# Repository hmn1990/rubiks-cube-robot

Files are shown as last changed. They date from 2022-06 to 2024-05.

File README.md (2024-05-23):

# 三阶魔方还原机器人

## 介绍
低成本魔方机器人设计。 含原理图、PCB、单片机源码（c语言）、结构图（openSCAD格式/STL格式）、主要器件BOM。 使用rp2040单片机控制，控制和魔方求解都使用单片机完成。 对于随机打乱的魔方，平均还原步骤数在21步左右。**扫描+计算+还原总时间在5.2秒左右。**  
2024-05-23主要更新内容：  
1.更换效率更高的魔方求解算法(感谢陈霜大神开源的min2phase，https://github.com/cs0x7f/min2phase.git)  
(1) 将使用java实现的min2phase改为使用c语言实现.  
(2) 测试10000个随机打乱的魔方,平均还原步骤数量由21.68步下降为20.25步.  
(3) 测试50个随机打乱的魔方,平均计算时间由180ms缩短为128ms.  
(4) 不需要NAND FLASH芯片W25N01,简化了设计,降低了成本.  
2.新增急停功能,在魔方还原过程中按下BUTTON_0或者1可以停止还原.  

2024-04-14主要更新内容：  
优化NAND FLASH刷写.刷写工具另开新仓库存放:  
https://gitee.com/hemn1990/uf2-nand-flash-prog  
以前的NAND FLASH刷写方式依旧可以使用.  
推荐使用新方式刷写NAND FLASH.  
新方式刷写时间更短,操作更简单.  

2024-03-28主要更新内容：  
优化求解魔方的程序,计算耗时减少1.5%.  
使用cube_robot.c里的debug_solve()测试  
STEP_LIMIT=23 P2_STEP_LIMIT_MAX=11 测试50个随机打乱的魔方，耗时8982ms  

2024-01-16主要更新内容：  
1.解决魔方安装错误时，容易死机的问题。  
2.修复使用还原功能后，立即使用自动测试功能，无法正确打乱魔方的问题。  
3.更新性能测试数据。  

2024-01-14主要更新内容：  
1.提升稳定性，可通过30轮的打乱+还原循环测试。测试30组不同的、使用CubeExplorer5.0的WCA打乱公式打乱的魔方，平均还原时间在5.2秒左右。作为对比，v2.0的平均还原时间在7.6秒左右。  
2.增加魔方打乱功能。  
3.增加打乱+还原自动测试功能  
4.移除无用还原动作。  
5.修改慢动作逻辑，操作方式改为短按SW4正常还原，长按SW4慢动作还原。  

2024-01-13主要更新内容：  
1.使用FIFO+PIO控制步进电机，支持三个电机以各自独立的速度曲线同时运动。  
2.改成只使用RP2040的一个核心，代码更容易被理解。  
3.提升I2C频率，顺便修复I2C1没有停止位的BUG。  
4.增加编译好的MCU固件cube_robot.uf2。  
5.优化还原速度，对每个动作设置各自独立的速度和加速度。  
6.优化还原速度，优化运动控制逻辑，支持同时执行某些动作，  

V2.0版本更新内容：  
1.提供原理图和PCB。  
2.解决滑台卡扣寿命短、容易断裂或者松动的问题，改为磁力固定。  
3.支持使用手机或者电脑的Type-C充电器供电。  
4.解决魔方夹持结构在长时间使用后容易松动、以及异常条件下可能断裂的问题。  
5.优化霍尔开关安装方式，简化安装步骤。  
6.解决棘轮结构噪声特别大的问题。  
7.提供详尽的装配教程，适合新手看的那种。  
8.完善物料清单。  
9.补充性能测试数据。  

后续更新计划：  
1.优化魔方还原算法。  

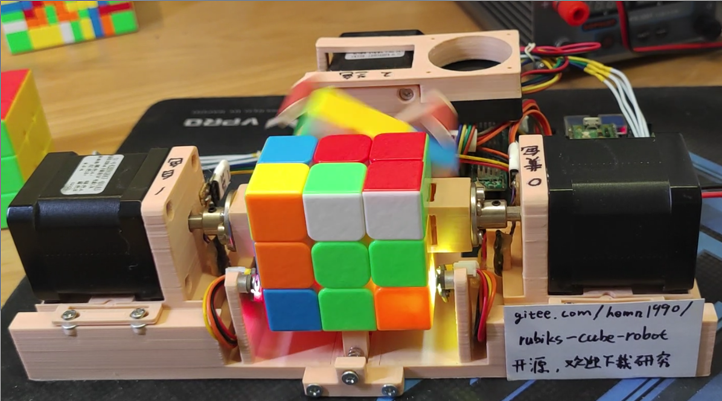
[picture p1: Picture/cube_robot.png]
Image text


V1.0版本演示视频：video/VID_20220618_165444.mp4  
V1.1版本（21步版本）的演示视频：http://www.bilibili.com/video/BV1Qt4y1476Y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  
V2.0版本的演示视频：https://b23.tv/s6q7KzU  
装配与调试教程：  
（1）控制板调试 https://b23.tv/Xj93aZk  
（2）魔方的选购 https://b23.tv/2x8Be0n  
（3）机械部分的组装 https://b23.tv/huJY1xt  
（4）整机调试 https://b23.tv/o8LBCXT  
（5）软件更新，10分钟搞定FLASH刷写 https://b23.tv/LJm5dEw  

## 关于硬件设计
2023-12-25更新：新增原理图与PCB设计文件  
2022-07-07更新：SPEPPER_EN修改为GP2，添加SPI NAND FLASH 型号W25N01GVZEIG  
2022-07-10更新：按键由GP0,GP1改为GP27,GP28)只修改了./src_21_step  

将RP2040单片机的GPIO，任意连接到步进电机驱动器、颜色传感器、霍尔传感器即可。除了SPI、UART，其他引脚只用了GPIO，未使用其他复用功能。  
霍尔传感器只能5V供电，RP2040单片机IO是3.3V，注意电平转换设计。  
FLASH是可选的，如果不使用FLASH，平均还原步骤数在32步左右。  
参考GPIO分配方式如下：  

#### 步进电机使能信号
- SPEPPER_EN    GP2
#### 步进电机控制信号
- SPEPPER_STEP0 GP11
- SPEPPER_DIR0  GP10
- SPEPPER_STEP1 GP9
- SPEPPER_DIR1  GP8
- SPEPPER_STEP2 GP7
- SPEPPER_DIR2  GP6
#### 霍尔开关，用于寻找零点
- HALL_0        GP5
- HALL_1        GP3
- HALL_2        GP4
#### 按键
- BUTTON_0      GP27
- BUTTON_1      GP28
#### 颜色传感器信号
- SDA0          GP14
- SCL0          GP15
- SDA1          GP12
- SCL1          GP13`
#### SPI NAND FLASH信号
- CS(1)         GP17
- DO(2)         GP16
- DI(5)         GP19
- CLK(6)        GP18

## 关于结构设计
1、推荐使用**ABS材料**3D打印，喷嘴0.4mm，层高0.2mm，顶层5层、底层5层、外壳4圈、填充20%-40%，生成支撑。  
## 单片机固件编译(./src_v3,平均还原步骤数在20步左右的版本，硬件上不需要外挂1Gbit FLASH)
修改CMakeLists.txt中的PICO_SDK_PATH，改为SDK的安装路径。  
````
# initalize pico_sdk from installed location
# (note this can come from environment, CMake cache etc)
set(PICO_SDK_PATH "/home/pi/pico/pico-sdk")
````
然后编译：  
````
cd ./src_v3/mcu
mkdir build
cd build
cmake ..
make
````
然后找到cube_robot.uf2，刷写到RP2040单片机即可。  
可以连接USB，使用minicom -D /dev/ttyACM0指令查看调试信息.  

## 单片机固件编译(./src_v2,平均还原步骤数在21步左右的版本)
推荐使用Linux系统进行开发，可按照RP2040官方文档中的脚本搭建开发环境。  
完成后，可额外安装pypy3，用于计算查找表。（此步骤可省略，提供生成好的）  
Windows也行，不过我没验证过。  

以Linux操作系统为例讲解,编译PR2040固件也可以使用Windows或者MacOS系统.  
参考raspberrypi官网搭建开发环境:  
https://www.raspberrypi.com/documentation/microcontrollers/rp2040.html  
也可以在b站搜索RP2040 SDK,找视频教程.  
搭建开发环境后,即可编译.  

**生成查找表**，并且进行验证（可选步骤,prog_flash目录下提供生成好的）  

运行完成后，得到lookup.dat,文件大小大约70MB  
````
cd ./src_v2/verify_on_pc
pypy3 prun.py
make
./solve
````

**编译单片机固件**
修改CMakeLists.txt中的PICO_SDK_PATH，改为SDK的安装路径。  
````
# initalize pico_sdk from installed location
# (note this can come from environment, CMake cache etc)
set(PICO_SDK_PATH "/home/pi/pico/pico-sdk")
````
然后编译：   
````
cd ./src_v2/mcu
mkdir build
cd build
cmake ..
make
````
然后找到cube_robot.uf2，刷写到RP2040单片机即可。  

可以连接USB，使用minicom -D /dev/ttyACM0指令查看调试信息，例如：  
````
color_detect: URUFUBDDUFRRFRDDFURLLLFUDLLLUBRDLRBFLDBDLBFFFBUBRBBRUD
Find 21 step solution in 139ms: B F' D' L' B F R B' U2 R B U2 B2 R2 U F2 D' B2 L2 U F2 
Totel time cost 7.772s: 
color_detect: UFFFURURRBDRRRDDLFBUDBFFBDFLBLLDBUBDFURLLRBUDUDLLBFRUL
Find 19 step solution in 95ms: F L2 B' R' L2 B L' B' F' D B2 D F2 D U B2 F2 L2 B2 
Totel time cost 7.575s: 

````
**刷写SPI NAND FLASH**
https://gitee.com/hemn1990/uf2-nand-flash-prog  
以前的NAND FLASH刷写方式依旧可以使用.  
推荐使用新方式刷写NAND FLASH.  
新方式刷写时间更短,操作更简单.  

以下为旧的方式：  
连接电脑和RP2040的串口，注意线一定要短，波特率高达1Mbps。   

按住BUTTON_0的同时给魔方机器人上电，程序会计算NAND FLASH的CRC32校验和，如果失败，自动进入刷写模式   
***注意烧写串口和USB虚拟串口不是同一个,不是同一个,不是同一个,重要的事情要说三遍.***   

````
cd ./src_21_step/prog_flash
make
./prog /dev/ttyS0 # /dev/ttyS0改为电脑的串口号

````
运行prog的电脑终端出现如下调试信息，说明刷写成功。
````
mcu in SPI FLASH programming mode
Check lookup.dat CRC32 = A8093698
0, size=131072
Erase Block 0
Program Block 0 ................................................................
Verify Block CRC32 0................................................................
此处省略若干行...
Erase Block 565
Program Block 565 ................................................................
Verify Block CRC32 565................................................................

````

## 单片机固件编译(./src_v1,平均还原步骤数在32步左右的版本，硬件上不需要外挂1Gbit FLASH)
*此版本不再维护，慎用*  
*与目前的硬件设计不完全匹配*  
推荐使用Linux系统进行开发，可按照官方文档中的脚本搭建开发环境。  
Windows也行，不过我没验证过。  

搭建好之后
````
cd src_v1
mkdir build
cd build
export PICO_SDK_PATH=xxxxxxxx
cmake ..
make
````
然后找到cube_robot.uf2，刷写到RP2040单片机即可。

可以连接USB，使用minicom -D /dev/ttyACM0指令查看调试信息，例如：
````
color_detect: FLDFUUUDBDLRURRFDLBFRDFBFLRDDURDBBUBLURBLRLBLFFUFBLDRU
stage=0, D' B U' L F' 
stage=1, B2 R2 U2 F2 D R' L' U L' 
stage=2, R2 D' F2 D2 R2 D R2 D' B2 D' 
stage=3, B2 R2 U2 B2 U2 L2 U2 L2 F2 R2 B2 
````

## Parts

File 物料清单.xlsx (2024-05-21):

整机物料：
物料名称 | 物料数量 | 备注
M3x6螺丝 | 12个 | 螺丝数量仅供参考，结构图没有绘制螺丝，可能有数漏的情况，建议多买些。 固定磁铁的4个必须用沉头的，其他的不限制。
M3x8螺丝 | 13个
M3x12螺丝 | 2个
M3x18螺丝 | 2个 | 固定风扇用的，有点长，M3x14更合适
M3滚花螺母(M3x4x5) | 11个 | 如果爪子部分使用3D打印+法兰联轴器，再加8个 外径5mm，螺纹M3，光杆直径4.3mm，高度4mm
M6垫片 | 4个 | 外径12mm，内径无所谓 必须选择能被磁铁吸引的材料，不能用不锈钢的
M3机米螺丝 | 6个 | 平头，3mm长度
直径2mm，长度15mm铁棒 | 1 | 对精度没有特殊要求，可搜索"车轴"等关键字购买 剪一段铁丝也行
线径0.4mm直径4.5mm长度10mm弹簧 | 1 | 实物如图
5mm法兰盘联轴器（内径5外径10） | 1 | 如果爪子部分使用3D打印+法兰联轴器，再加2个
42步进电机 | 3 | 48mm长度,额定电流≥1.5A
A3144霍尔传感器 | 3 | 直插的
TCS3472颜色传感器模块 | 2 | 如图
导线 | 若干 | 推荐24AWG的
XH-2Y 2.54mm间距插头 | 1 | 压接在风扇上，如果风扇本身就是这种接口，就不用了。
XH-3Y 2.54mm间距插头 | 6 | 用于制作霍尔传感器的线
XH-3A 2.54mm间距插座 | 3 | 焊接A3144霍尔传感器，然后粘在电机座上
XH-4A 2.54mm间距插头 | 3 | 制作电机线，如果电机本身就是这种接口，就不用了
4010风扇 | 1 | 24V电压的，可选，不长时间使用可以不加风扇
3D打印耗材 ABS | 一卷 | 实际用量300g左右 不推荐用PLA，尤其是夹持魔方的结构 PETG可能也行，但是我没验证过
泡棉 | 一卷 | 可选，用于电机减震，5mm宽度，1mm厚度 不用也可以
塑料垫柱 | 4个 | 2-3mm高度，用于固定颜色传感器，也可以3D打印，提供3D打印STL文件
润滑油 | 少量 | 可选，买魔方时可能会送 1、用于润滑魔方中心轴 2、用于润滑魔方机器人的可动部件
螺纹胶 | 少量 | 可选，用于固定容易松动的机米螺丝
热熔胶 | 少量 | 可选，加固霍尔传感器
尼龙扎带 | 少量 | 可选，用于整理线缆
方形锅磁 | 2个 | 尺寸如图，孔距是30mm
三阶魔方 | 1个 | 边长56mm，推荐带磁力的 爪子部分的图纸，是按照圣手三阶磁力魔方绘制的 选择其他魔方，可能需要根据实测尺寸修改。
充电头 + Type-C接口线缆 电脑或者手机的都可以 | 1套 | 至少30W，支持 PD3.0/2.0或者BC1.2快充协议 并且使用该协议时，输出功率能达到至少30W。 测试过小米的55W和90W充电器。
直流电源（与Type-C电源，二选一） | 1个 | 12V-20V的都可以，推荐2A或者以上电流的。
6061铝条 | 1条 | 20 x 20mm x 200mm
磁铁 | 3个 | 直径6mm，厚度2-3mm
PCBA上的元器件：
型号 | 数量 | 位号 | 备注
印制板 | 1 | 无 | Gerber_PCB1_2023-12-20.zip
100nF 25V 0603电容 | 31 | C1,C2,C4,C5,C6,C7,C8,C9,C11,C13,C14,C15,C16,C17,C18,C19,C21,C22,C23,C24,C25,C27,C28,C29,C30,C31,C33,C34,C35,C42,C43
1uF 6.3V 0603电容 | 3 | C3,C12,C39
27pF 50V 0603电容 | 2 | C10,C40
220nF 16V 0603电容 | 3 | C20,C26,C32
330uF 25V直插电解电容 | 4 | C36,C37,C38,C44 | 尺寸8x12mm
10uF 6.3V 0603电容 | 2 | C45,C46
XH-4A插座（2.54mm间距） | 5 | CN1,CN3,CN8,CN9,CN10
XH-3A插座（2.54mm间距） | 3 | CN2,CN4,CN5
XH-2A插座（2.54mm间距） | 1 | CN12
1N5819W | 5 | D1,D2,D3,D4,D5 | 丝印S4 SOD123封装
2.54mm间距单排针 | 2 | H1,H2 | 掰成3pin的使用
0805 LED | 4 | LED1,LED2,LED3,LED4 | 调试用的，颜色不限
5.1kΩ 0603电阻 | 9 | R1,R2,R12,R13,R14,R15,R30,R40,R50
1k 0603电阻 | 7 | R4,R7,R8,R9,R10,R11,R52
27.4Ω 0603电阻 | 2 | R5,R6
10kΩ 0603电阻 | 11 | R16,R17,R18,R22,R23,R24,R35,R36,R45,R46,R53
100mΩ 0805电阻（100mΩ=0.1Ω） | 6 | R19,R20,R32,R33,R42,R43
0Ω 0603电阻 | 13 | R21,R25,R28,R29,R34,R37,R38,R39,R44,R47,R48,R49,R55
8.2kΩ 0603电阻 | 3 | R31,R41,R51
直插6x6微动开关 | 4 | SW1,SW2,SW3,SW4
RP2040 | 1 | U1 | LQFN-56
W25Q16JVSNIQ | 1 | U2 | SOP-8
W25N01GVZEIG | 1 | U5 | WSON-8
HR4988E(实际购买的HR4988SQ) | 3 | U6,U7,U8 | QFN-28
CH224K | 1 | U9 | ESSOP-10
AMS1117-3.3 | 1 | U12 | SOT-223
L7805CV-DG | 1 | U13 | TO-220-3
16PIN TYPE-C 母座 | 2 | USB1,USB2 | 注意尺寸，买和PCB封装对应的 外观如图
12MHz 49S直插无源晶振 | 1 | X1
9x9x12mm 散热器 | 3 | 无

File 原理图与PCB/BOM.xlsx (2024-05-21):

型号 | 位号 | 数量 | 备注
100nF 25V 0603电容 | C1,C2,C4,C5,C6,C7,C8,C9,C11,C13,C14,C15,C16,C17,C18,C19,C21,C22,C23,C24,C25,C27,C28,C29,C30,C31,C33,C34,C35,C42,C43 | 31
1uF 6.3V 0603电容 | C3,C12,C39 | 3
27pF 50V 0603电容 | C10,C40 | 2
220nF 16V 0603电容 | C20,C26,C32 | 3
330uF 25V直插电解电容 | C36,C37,C38,C44 | 4 | 尺寸8x12mm
10uF 6.3V 0603电容 | C45,C46 | 2
XH-4A插座 | CN1,CN3,CN8,CN9,CN10 | 5
XH-3A插座 | CN2,CN4,CN5 | 3
XH-2A插座 | CN12 | 1
1N5819W | D1,D2,D3,D4,D5 | 5 | 丝印S4 SOD123封装
2.54mm间距单排针 | H1,H2 | 2 | 掰成3pin的使用
0805 LED | LED1,LED2,LED3,LED4 | 4 | 调试用的，颜色不限
5.1kΩ 0603电阻 | R1,R2,R12,R13,R14,R15,R30,R40,R50 | 9
1k 0603电阻 | R4,R7,R8,R9,R10,R11,R52 | 7
27.4Ω 0603电阻 | R5,R6 | 2
10kΩ 0603电阻 | R16,R17,R18,R22,R23,R24,R35,R36,R45,R46,R53 | 11
100mΩ 0805电阻（100mΩ=0.1Ω） | R19,R20,R32,R33,R42,R43 | 6
0Ω 0603电阻 | R21,R25,R28,R29,R34,R37,R38,R39,R44,R47,R48,R49,R55 | 13
8.2kΩ 0603电阻 | R31,R41,R51 | 3
直插6x6微动开关 | SW1,SW2,SW3,SW4 | 4
RP2040 | U1 | 1 | LQFN-56
W25Q16JVSNIQ | U2 | 1 | SOP-8
W25N01GVZEIG | U5 | 1 | WSON-8
HR4988E(实际购买的HR4988SQ) | U6,U7,U8 | 3 | QFN-28
CH224K | U9 | 1 | ESSOP-10
AMS1117-3.3 | U12 | 1 | SOT-223
L7805CV-DG | U13 | 1 | TO-220-3
16PIN TYPE-C 母座 | USB1,USB2 | 2 | 注意尺寸，买和PCB封装对应的
12MHz 49S直插无源晶振 | X1 | 1
9x9x12mm 散热器 | 无 | 3

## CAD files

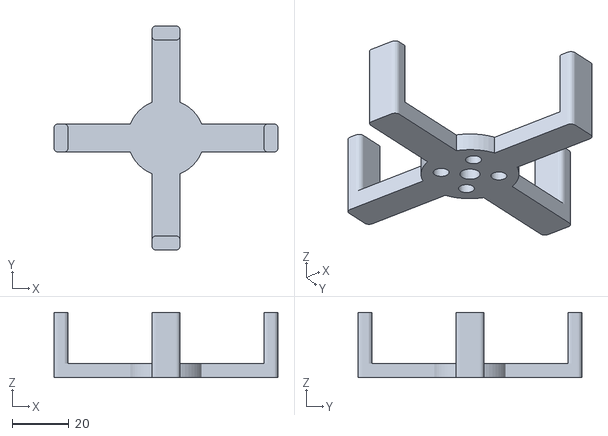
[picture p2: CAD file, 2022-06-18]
3D_print_STL/3d_print_cube_spin.stl
79.0 x 79.0 x 23.0

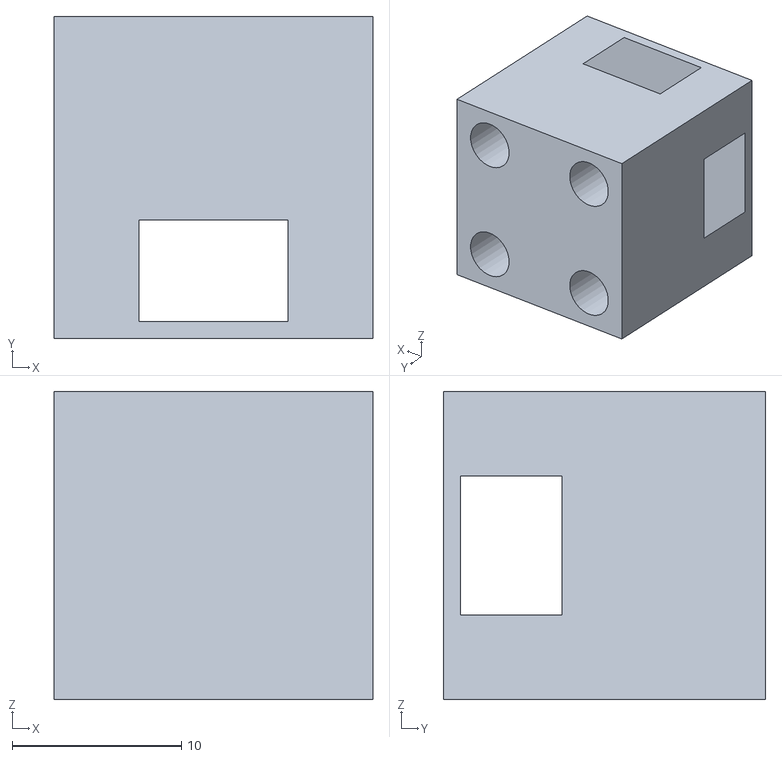
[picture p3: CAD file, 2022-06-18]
3D_print_STL/爪子_v11版本3D打印x2.stl
18.8 x 19.0 x 18.2

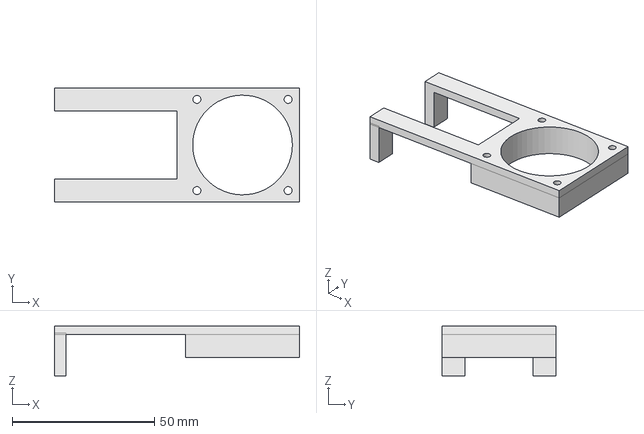
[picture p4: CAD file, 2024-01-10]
STEP/fan_holder.step
86.0 x 40.0 x 17.5 mm

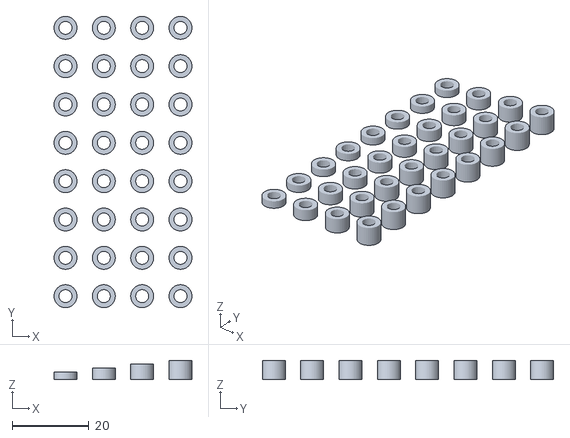
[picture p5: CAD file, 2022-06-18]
3D_print_STL/cylinder_reserve.stl
36.0 x 76.0 x 5.00

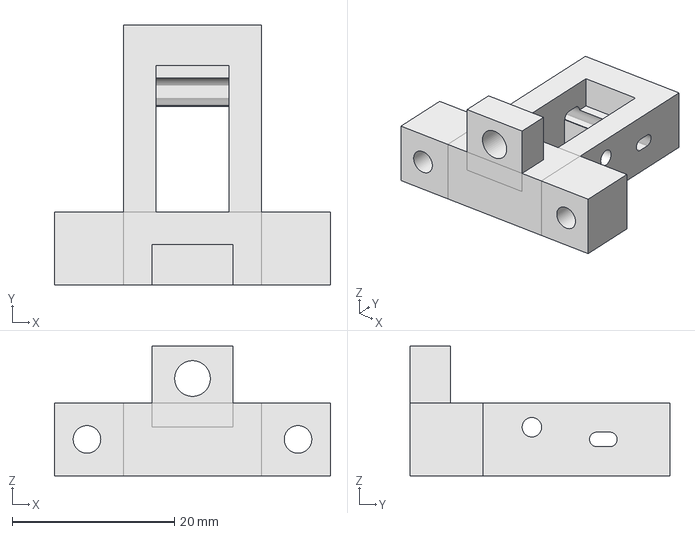
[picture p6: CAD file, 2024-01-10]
STEP/棘轮部件2.step
34.0 x 32.0 x 16.0 mm

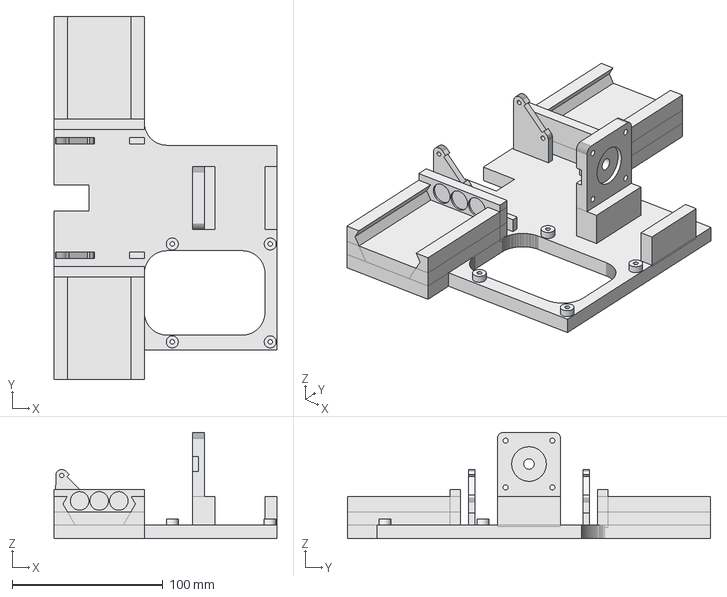
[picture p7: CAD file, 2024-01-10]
STEP/主体部分.step
148.0 x 241.0 x 70.5 mm

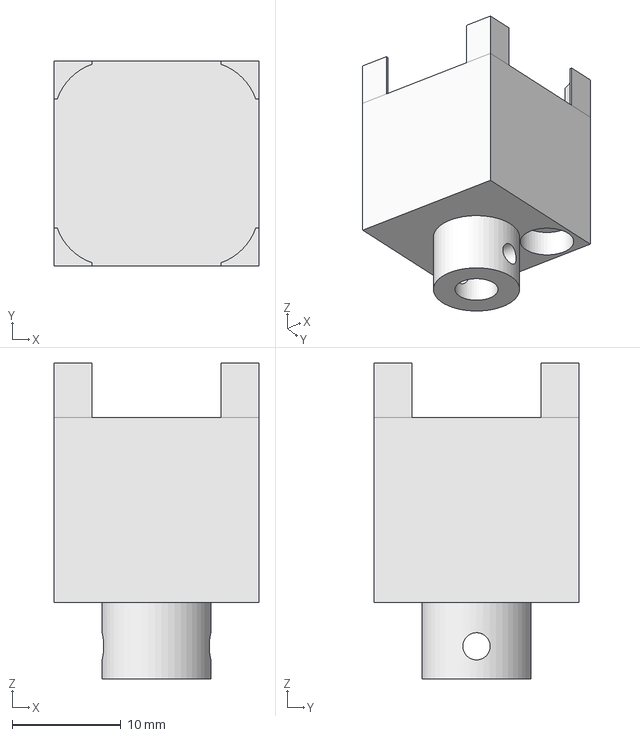
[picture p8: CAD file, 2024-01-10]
STEP/爪子-铣加工x2.step
18.8 x 18.8 x 29.0 mm

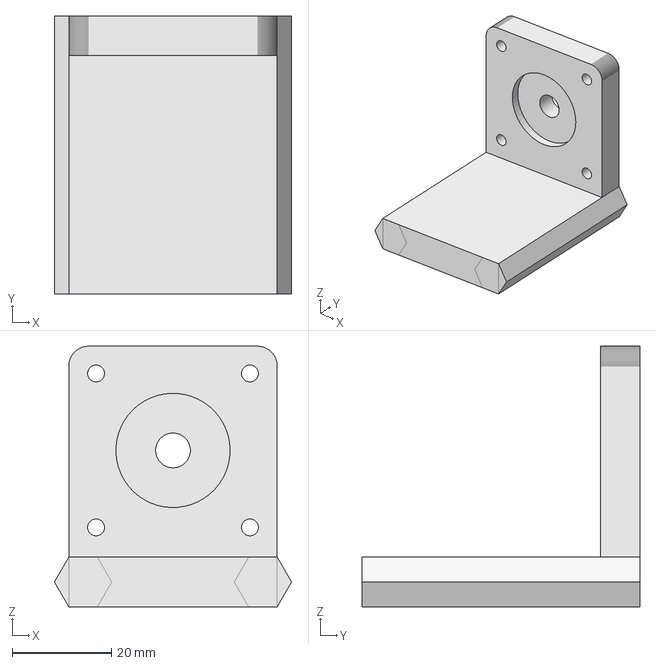
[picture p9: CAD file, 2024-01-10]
STEP/电机架1.step
47.8 x 56.0 x 52.5 mm

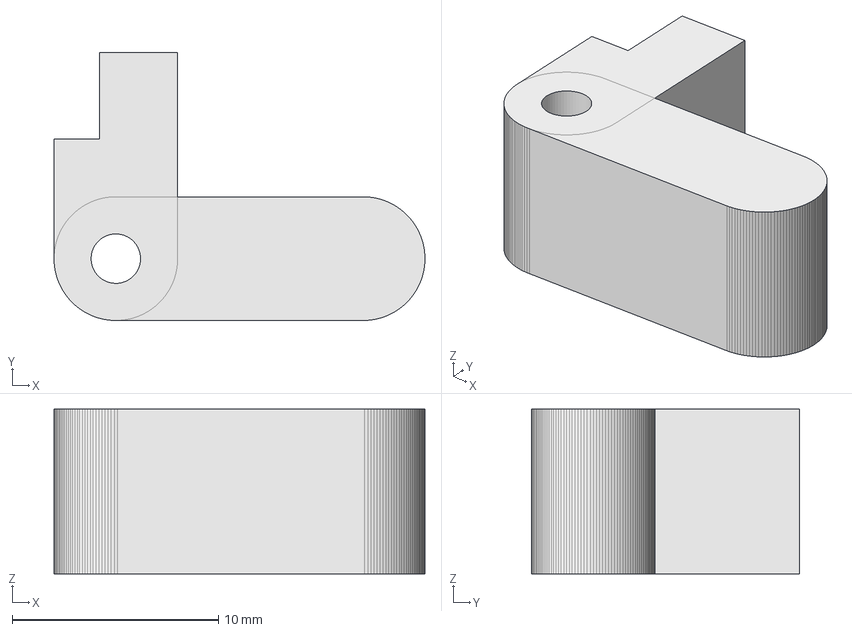
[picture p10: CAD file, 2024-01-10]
STEP/棘轮部件1.step
18.0 x 13.0 x 8.00 mm

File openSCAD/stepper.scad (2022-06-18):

$fa=6;
$fs=0.5;



stepper42();
translate([0,0,23]) rotate([180,0,0]) flange();
module flange(){
    difference(){
        union(){
            cylinder(h=2,d=22);
            cylinder(h=12,d=10);
        }
        cylinder(h=99,d=5,center=true);
        translate([8,0,0]) cylinder(h=99,d=3,center=true);
        translate([-8,0,0]) cylinder(h=99,d=3,center=true);
        translate([0,-8,0]) cylinder(h=99,d=3,center=true);
        translate([0,8,0]) cylinder(h=99,d=3,center=true);
    }
}


module stepper42(){
    union(){
        top();
        translate([0,0,-8]) mid();
        translate([0,0,-8-9.5-23-8]) mirror([0,0,1]) bot();
    }
}


module mid(){
    mid_r = 8;
    offset_xy = 42/2 - mid_r;
    length = 23+8; // 硅钢片高度
    hull(){
        translate([offset_xy, offset_xy, -length]) cylinder(h=length, r=mid_r, $fn=4);
        translate([offset_xy, -offset_xy, -length]) cylinder(h=length, r=mid_r, $fn=4);
        translate([-offset_xy, offset_xy, -length]) cylinder(h=length, r=mid_r, $fn=4);
        translate([-offset_xy, -offset_xy, -length]) cylinder(h=length, r=mid_r, $fn=4);
    }
}
module top(){
    top_r = 4;
    offset_xy = 42/2 - top_r;
    length = 23+2; // 电机轴长度
    union(){
        difference(){
            hull(){
                translate([offset_xy, offset_xy, -8]) cylinder(h=8, r=top_r, $fn=4);
                translate([offset_xy, -offset_xy, -8]) cylinder(h=8, r=top_r, $fn=4);
                translate([-offset_xy, offset_xy, -8]) cylinder(h=8, r=top_r, $fn=4);
                translate([-offset_xy, -offset_xy, -8]) cylinder(h=8, r=top_r, $fn=4);
            }
            translate([31/2, 31/2, 0]) cylinder(h=20,d=2.5,center=true); 
            translate([-31/2, 31/2, 0]) cylinder(h=20,d=2.5,center=true);
            translate([31/2, -31/2, 0]) cylinder(h=20,d=2.5,center=true);
            translate([-31/2, -31/2, 0]) cylinder(h=20,d=2.5,center=true);       
        }
        difference(){
            cylinder(h=2,d=22);
            cylinder(h=20,d=9,center=true);
        }
        difference(){
             cylinder(h=length,d=5);
             translate([-5/2, 4.5/2, 0]) cube([5,5,length]);
        }
    }
}
module bot()
{
    bot_r = 4;
    offset_xy = 42/2 - bot_r;
    union(){
        difference(){
            hull(){
                translate([offset_xy, offset_xy, -9.5]) cylinder(h=9.5, r=bot_r, $fn=4);
                translate([offset_xy, -offset_xy, -9.5]) cylinder(h=9.5, r=bot_r, $fn=4);
                translate([-offset_xy, offset_xy, -9.5]) cylinder(h=9.5, r=bot_r, $fn=4);
                translate([-offset_xy, -offset_xy, -9.5]) cylinder(h=9.5, r=bot_r, $fn=4);
            }
            translate([31/2, 31/2, 0]) cylinder(h=20,d=3.5,center=true); 
            translate([-31/2, 31/2, 0]) cylinder(h=20,d=3.5,center=true);
            translate([31/2, -31/2, 0]) cylinder(h=20,d=3.5,center=true);
            translate([-31/2, -31/2, 0]) cylinder(h=20,d=3.5,center=true);
            translate([31/2, 31/2, -2.5]) cylinder(h=20,d=6); 
            translate([-31/2, 31/2, -2.5]) cylinder(h=20,d=6);
            translate([31/2, -31/2, -2.5]) cylinder(h=20,d=6);
            translate([-31/2, -31/2, -2.5]) cylinder(h=20,d=6);
            translate([0, 0, -3.5]) cylinder(h=20,d=9);
        }
        translate([-16/2,42/2,-9.5])cube([16,6,9.5]);
    }
}

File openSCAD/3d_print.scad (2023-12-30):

$fa=6;
$fs=0.5;
use <main.scad>



// 打印1个
base_board();

// 打印1个,和V1.1一样
//cube_spin();

// 打印1个,和V1.1一样
// rotate([180,0,0]) fan_holder();

// 建议使用 爪子-铣加工.scad中的铣加工版本
// 移除3D打印版本，如果需要，可将main.scad中的相关代码取消注释
//claw_3d_print();

// 打印1个
//stepper_shelf(0, 0);

// 打印1个
//stepper_shelf(0, 1);

// 打印1个
//rotate([0,90,0])cube_block_move();
// 打印1个
//cube_block_fixed();

// 垫柱，打印不同尺寸的备用
/*
for(i=[0:7]){
    translate([10*0,i*10,0])cyl(2);
    translate([10*1,i*10,0])cyl(3);
    translate([10*2,i*10,0])cyl(4);
    translate([10*3,i*10,0])cyl(5);
}
*/

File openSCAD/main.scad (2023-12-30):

use <stepper.scad>
use <rubik_cube.scad>

//rotate([90,0,0]) stepper42();

$fa=6;
$fs=0.5;
// 滚花螺母孔径，需要比滚花螺母直径略小一点
m3_nut_hole_d = 4.4;
// m3螺丝孔，直接把螺丝拧到塑料件里
m3_hole_d = 2.8;
// 魔方旋转角度
cube_rotate=0; //0 78 45


// ------------------------------------------------------------------
//夹持魔方的结构，需要根据使用的魔方调整形状
//对强度要求较高，使用FDM原理的3D打印机，需要注意打印方向，4个孔面向X或者Y方向都行
//可以微调尺寸，解决3D打印ABS小尺寸零件时变形的问题
//根据打印机情况和使用的耗材类型调整（使用PLA的话不用调，基本不变形，但是强度很低）
//claw_3d_print();
/*
claw_size_x=18.7+0.1;
claw_size_y=18.7-0.5;
claw_r=5;

module claw_3d_print()
{
    rotate([90,0,0]){
        // 固定魔方的爪子，打印2个
        claw();
        //支撑，打完割掉
        translate([-claw_size_x/2,-claw_size_y/2, 18]) cube([claw_size_x,claw_size_y,1]); 
    }
}

module claw(){
    difference(){
        union(){
            translate([-claw_size_x/2, -claw_size_y/2, 0 ]) cube([claw_size_x,claw_size_y,12]);
            translate([-claw_size_x/2, -claw_size_y/2, 12]) claw_1(0);
            translate([claw_size_x/2,  -claw_size_y/2, 12]) claw_1(1);
            translate([claw_size_x/2,  claw_size_y/2,  12]) claw_1(2);
            translate([-claw_size_x/2, claw_size_y/2,  12]) claw_1(3);
        }
        union(){
            for(i=[0:3]){
                rotate([0,0,45+90*i]) {
                    translate([8,0,0]) cylinder(h=7, d=m3_nut_hole_d);
                }
            }
        }
    }
}

module claw_1(dir)
{
    rotate([0,0,dir*90]){
        difference(){
            cube([claw_r, claw_r, 6]);
            translate([claw_r, claw_r, 0]) cylinder(h=6,r=claw_r);
        }
    }
}
*/
// ------------------------------------------------------------------
//夹持魔方的结构，需要根据使用的魔方调整形状，铣加工版本
// m3螺丝孔，需要使用丝锥攻丝
m3_hole = 2.5;
claw_size_x=18.8;
claw_size_y=18.8;
claw_r=5.2;
claw_height=5;
module claw(){
    difference(){
        union(){
            translate([-claw_size_x/2, -claw_size_y/2, 0 ]) cube([claw_size_x,claw_size_y,17]);
            translate([-claw_size_x/2, -claw_size_y/2, 17]) claw_1(0);
            translate([claw_size_x/2,  -claw_size_y/2, 17]) claw_1(1);
            translate([claw_size_x/2,  claw_size_y/2,  17]) claw_1(2);
            translate([-claw_size_x/2, claw_size_y/2,  17]) claw_1(3);
            translate([0, 0, -7]) cylinder(h=7,r=5);
        }
        // 电机轴
        translate([0, 0, -7 ]) cylinder(h=13,r=2.5);
        // 磁铁位置
        translate([8.1/sqrt(2)+0.1, 8.1/sqrt(2)+0.1, 0]) cylinder(h=3,r=3.1);
        // 顶丝孔
        translate([0,0,-7+3]) rotate([0,90,0]) cylinder(h=50,r=m3_hole/2,center=true);
    }
    
}
// 一个爪子
module claw_1(dir){
    rotate([0,0,dir*90]){
        difference(){
            cube([3.5, 3.5, claw_height]);
            translate([claw_r, claw_r, 0]) cylinder(h=claw_height,r=claw_r);
        }
    }
}
// ------------------------------------------------------------------
// 可活动步进电机支架 打印2个
module m3_hole(len1=10, len2=3)
{
    union(){
        translate([0,0,len2]) cylinder(h=len1, d=3.4);
        cylinder(h=len2, d=6);
    }
}

module stepper_shelf(style=0,sensor=0){
    union(){
        // 固定步进电机
        translate([0,0,42/2+0.5]) rotate([90,0,0]){
            difference(){
                hull(){
                    dst = 42/2-4;
                    translate([-dst,dst,0]) cylinder(h=8,r=4);
                    translate([dst,dst,0])  cylinder(h=8,r=4);
                    translate([-dst,-dst-0.5,4]) cube(8,center=true);
                    translate([dst,-dst-0.5,4])  cube(8,center=true);
                }
                translate([31/2, 31/2, 0])  m3_hole(10,3);
                translate([-31/2, 31/2, 0]) m3_hole(10,3);
                translate([31/2, -31/2, 0]) m3_hole(10,3);
                translate([-31/2, -31/2, 0])m3_hole(10,3);
                translate([0, 0, 8-2-0.5]) cylinder(h=10,d=22+1);
                cylinder(h=20,d=7,center=true);
                // 霍尔安装位置
                if(sensor == 0){
                    translate([(42-10.2)/2, 0, 4/2])cube([10.2,10.2,4],center=true);
                }else{
                    translate([-(42-10.2)/2, 0, 4/2])cube([10.2,10.2,4],center=true);
                }
            }
        }
        // 滑块
        if(style == 0){
            size_x = 42;
            size_y = 48+8;
            height = 10;
            r1 = height/2/sin(60);
            difference(){
                union(){
                    translate([-size_x/2+r1/2,-size_y/2,-height/2]) rotate([90,0,0]) 
                        cylinder(size_y, r=r1, center=true, $fn=6);
                    translate([size_x/2-r1/2,-size_y/2,-height/2]) rotate([90,0,0]) 
                        cylinder(size_y, r=r1, center=true, $fn=6);
                    translate([0,-size_y/2,-height/2]) 
                        cube([size_x,size_y,10],center=true);
                }
                translate([ 15,0.1,-2.5]) rotate([90,0,0]) cylinder(h=5,d=m3_nut_hole_d);
                translate([-15,0.1,-2.5]) rotate([90,0,0]) cylinder(h=5,d=m3_nut_hole_d);
            }
        }
        // 固定电机，不可活动
        if(style == 1){
            size_x = 42;
            size_y = 48+8+5;
            height = 20;
            translate([0,-(size_y-40)/2+3,-height/2])
                cube([size_x,15,height],center=true);
            translate([0,-52,-height/2])
                cube([size_x,8,height],center=true);
        }
    }
}


// ------------------------------------------------------------------
// 用于旋转魔方的十字结构
// 对强度要求较高，适当提高填充和壁厚
module cube_spin()
{
    difference(){
        union(){
            translate([0,0,2.5]) cube([72,10,5],center=true);
            translate([0,0,2.5]) rotate([0,0,90]) cube([72,10,5],center=true);
            cylinder(h=5,d=27);
            for(i=[0:3]){
                rotate([0,0,90*i]) {
                    //translate([64/2+5,-5,0]) cube([5,10,23]);
                    hull(){
                       translate([38,5-1.5,0]) cylinder(h=23,r=1.5);
                       translate([38,-5+1.5,0]) cylinder(h=23,r=1.5);
                       translate([38-2,5-1.5,0]) cylinder(h=23,r=1.5);
                       translate([38-2,-5+1.5,0]) cylinder(h=23,r=1.5);
                    }
                }
            }
        }
        for(i=[0:3]){
            rotate([0,0,45+90*i]) {
                translate([8,0,-0.5]) cylinder(h=5, d=m3_nut_hole_d);
            }
        }
        translate([0,0,-0.5]) cylinder(h=5, d=5.6);
    }
}

// ------------------------------------------------------------------
// 使魔方中间层只能单向旋转的部件
module cube_block(){
    cube_block_fixed();
    cube_block_move();
}
module cube_block_fixed(){
    difference(){
        union(){
            // 主体
            difference(){
                translate([0,1,-1.5]) cube([17,32,9],center=true);
                translate([0,3,0]) cube([9,18,99],center=true);
                rotate([0,-90,0]) cylinder(h=99,d=2.4,center=true);
            }
            // 底部限位
            translate([-5,7,-6]) cube([10,9,4.5]);
        }
        hull(){
            translate([0,8,-1.5])rotate([0,-90,0]) cylinder(h=99,d=1.8,center=true);
            translate([0,8+1.6,-1.5])rotate([0,-90,0]) cylinder(h=99,d=1.8,center=true);
        }
    }
    // 弹簧固定器
    difference(){
        translate([-5,-15,0]) cube([10,5,10]);
        translate([0,0,6]) rotate([90,0,0]) cylinder(h=99,d=m3_nut_hole_d);
    }
    // 固定螺丝孔，两个M3通孔
    difference(){ 
        translate([0,-10.5,-1.5]) cube([34,9,9],center=true);
        translate([-13,30,-1.5]) rotate([90,0,0]) cylinder(h=99,d=3.4);
        translate([13,30,-1.5]) rotate([90,0,0]) cylinder(h=99,d=3.4);
    }
}
module cube_block_move(){
    translate([4,0,0]) rotate([0,-90,0]) difference(){
        union(){
            hull(){
                translate([18-6,0,0]) cylinder(h=8,d=6);
                cylinder(h=8,d=6);
            }
            hull(){
                translate([-3,5,0]) cube([6,5,8]);
                cylinder(h=8,d=6);
            }
        }
        translate([-3-0.2,6-0.2,0-0.2]) cube([2+0.4,5+0.4,8+0.4]);
        cylinder(h=99,d=2.4,center=true);
    }
}
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

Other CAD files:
STEP/cube_spin.step
STEP/电机架0.step
openSCAD/rubik_cube.scad
3D_print_STL/fan_holder.stl
3D_print_STL/主体部分.stl
3D_print_STL/棘轮部件1.stl
3D_print_STL/棘轮部件2.stl
3D_print_STL/爪子-铣加工x2.stl
3D_print_STL/电机架0.stl
3D_print_STL/电机架1.stl
openSCAD/爪子-铣加工.scad

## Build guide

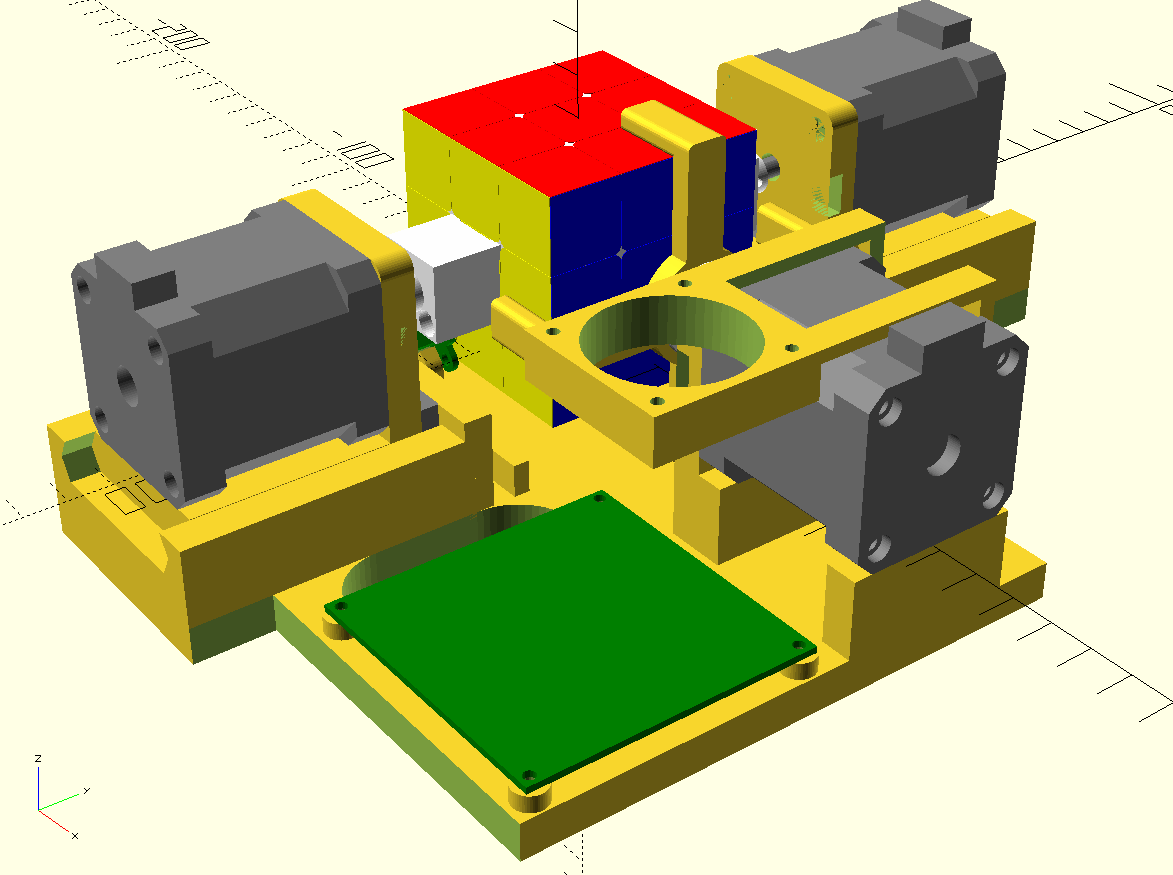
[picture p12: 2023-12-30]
装配图-V20-后面.PNG

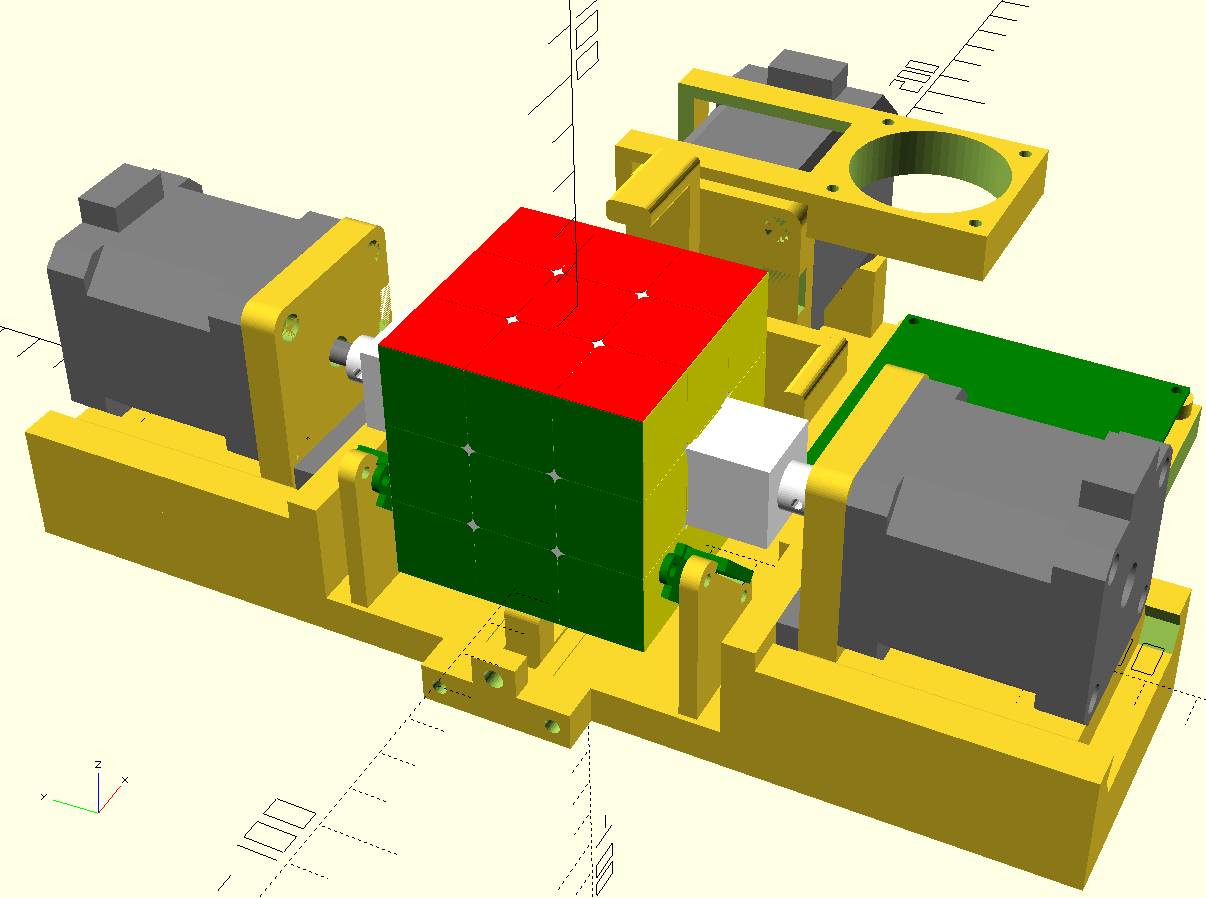
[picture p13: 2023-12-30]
装配图-V20-前面.PNG

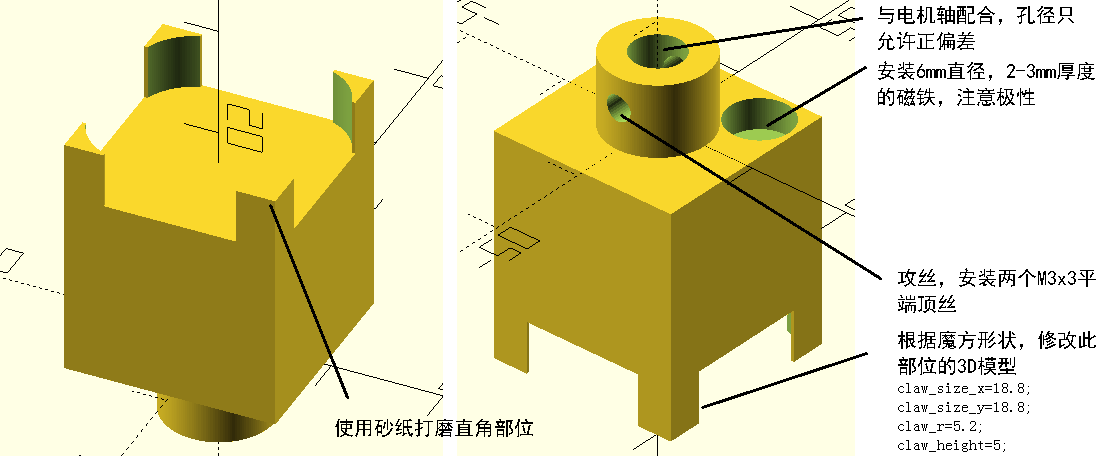
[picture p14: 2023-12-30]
3D_print_STL/爪子-铣加工-说明.png

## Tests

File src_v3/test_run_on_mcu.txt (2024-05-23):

Init.
test: URBUUURBFDBDURFDFDURLBFLBDRUBFRDLFRBRFBLLLUFLLUFDBDRDL
Find 18 step solution in 164ms: U' B2 D  R' L' D2 B  L  B  D2 R2 L2 F' U2 D2 F' U  F2 
test: LDFLUBLLUFULFRRRRFBBLUFRBDFRBDUDBRDRDFUDLFDLUDRBUBFULB
Find 21 step solution in 115ms: B2 L  B' R' F' D  B' R' F2 R2 D2 R2 B  U2 L2 B' R2 F' B2 R2 D  
test: UFULUBDFLDDLLRRLRRRRBUFFLRUFUBLDDDUUBDBLLFRUDFDRBBBFBF
Find 21 step solution in 46ms: U  R  B  U  L2 U  L  B' R' D2 L2 B2 U' L2 U' F2 R2 L2 U2 L2 F2 
test: UULDURUDBDFBURLDBRLLRLFRFDRLBFRDRLLBRFBULUDDUDBFBBFUFF
Find 21 step solution in 71ms: U  D  R2 B2 R' F' R  D' B  U2 D' F2 L2 D  L2 D  R2 D2 F2 R2 B2 
test: BDLUURLDRUBDDRFLLRBRBLFFDUFFRULDBLFUDBUFLUBDRFBRRBUFLD
Find 22 step solution in 227ms: U2 L' D' F' U  B' R' U  F2 R2 L2 U  L2 U  F2 B2 U  B2 U2 B' U2 R' 
test: RULDUFRLULDDBRFRRFDDBUFRDLBRUULDUBRUFRFBLFDBBFBULBDLFL
Find 21 step solution in 106ms: D  F' D2 R  F2 L' B2 D2 U2 R' D2 B2 L  F2 D' R2 U  L' B2 U' F  
test: RBDBULFFDLDLBRUBBBLRFUFLULRRFDFDDBDLDRUULLUDFBUFRBFURR
Find 20 step solution in 166ms: R' U2 D' R2 U  R' B  R  D2 L2 U2 F2 L2 B2 D2 R  B2 L' B' D  
test: BLLUULBULUUDLRDBDBDBFLFFDUUFRRRDRFFLLFRDLBRBRFDDBBFURU
Find 20 step solution in 117ms: D  B' R  D2 F2 B2 R  L2 U2 R2 F  D2 B  L2 B' R2 B' L2 U  B  
test: BFDBUBFDUFDLRRBRLLRRLLFUUDDLLBFDURDDRLDULFUUBBRURBBFFF
Find 20 step solution in 182ms: B' R' B2 L' U  L2 F' D2 B  U2 R  B2 D2 L2 D2 R' L2 F2 U2 L  
test: DBFRUUUURULLLRBBRDFFBDFDFLLUFUUDUDFLFFLDLBBBRDLRRBRBDR
Find 20 step solution in 88ms: F2 U2 B2 D' B2 D  L2 U  F2 R2 U' L  F' L2 D  U  L' B' D' B' 
test: UFRUUUFRLFLUDRDBDDRFDBFRBBDUULBDLRUBFRDBLDBLLFLLFBRRFU
Find 21 step solution in 157ms: F  L' F2 D' U' L2 D2 L2 F2 L2 U' F2 L2 U' L' B' D2 L' B' R  B  
test: LBRFUDRBDLLUFRLRDRDDFLFDBBDULBUDRBBBURFULUDFLFRFFBRUUL
Find 21 step solution in 152ms: D' L2 F2 R  U2 F2 L' B2 L  D2 F2 U2 F2 B' U  R' F2 L' D' R2 B  
test: DUDUUBFDBLRBFRBUBFURDDFLRFBUULLDULFDLLRFLLFBBRRFDBDRRU
Find 18 step solution in 83ms: F  D  F' L2 U  F2 R' D2 B2 U' R2 U  R2 D' L2 U  R  D2 
test: BBDFUULDFRRLRRRDURBBDLFDULFRDLUDFFDDRLURLUUBFBLUFBBBFL
Find 20 step solution in 57ms: L' B2 L2 D  F2 D  B2 D' R2 U  L2 F2 D2 L' F' R  F' U  R  D2 
test: BBBFULRUBUURFRRRDFDFLUFDLRUUUFFDRLDLRRFLLBBLFDLUBBDDBD
Find 20 step solution in 113ms: L  D  F2 U2 L2 D  B2 U2 L2 B2 F2 D  R  D2 R  F' L  F' L2 D  
test: RURFULBFBUBBDRRFDLDLLFFRLRRFUUDDLBUFDRRLLDDBDUBFBBUUFL
Find 19 step solution in 50ms: U2 D  F2 R2 D2 R2 F  U' L  U2 F  R2 B  R2 L2 D2 L2 F' U2 
test: LBRDUDRBLDLUFRUULLBUBRFUUFRLRBDDFFUFFFDBLBDRBFDDRBLULR
Find 20 step solution in 138ms: F' R2 U' L' D' R  F2 U' B' R  L  F2 L' B2 L' D2 B2 D2 F2 R2 
test: DULLUFLBBDRUFRBRURDRRRFLRDBFFUDDLFFFLDBULDUBUBRFLBBDUL
Find 20 step solution in 232ms: L  D' L  U' L2 U  B  R  U  F' L  B2 R' L' U2 R  U2 F2 L' F2 
test: BFFUULRBDLDURRLDBRDLFFFURDLFRBBDRUUBDBFULDBDULRRFBLUFL
Find 21 step solution in 180ms: B' R' U2 F  B  U' L' D' F2 B2 D' B2 D' B2 L2 D2 R2 D' B' R2 U' 
test: LLRRULRBRFBFRRDBRUUUUUFFFFDLDLBDDDFBFUBBLLBDUDFDLBRLUR
Find 21 step solution in 158ms: L' B' L  D2 R  U2 L  D2 L2 D2 B2 R  F2 R' D  L' U  R2 D' L2 B' 
test: LBBLULLDFUFUURURUUURRRFBRBFBRDLDFLDBDDFFLUDBDRDBLBRLFF
Find 20 step solution in 66ms: F  U2 F  B2 R' D  F' B' U' L2 D2 F' L2 D2 F' L2 B' R2 D2 B  
test: RUUBUUDDUBLLLRRFRUFRRBFDLULDRDFDBUUFBDRFLLBDBFBDFBLRFL
Find 19 step solution in 41ms: L2 F  L2 F  D  R' D  R  L' D2 L2 U2 L2 B' L2 F  B  R2 B  
test: RRDDUFBBBUDBRRDDBRLLLFFULLRUUFRDUDFUULDFLUFDFRBBBBRFLL
Find 19 step solution in 68ms: U  D  L  U  L  U2 F  D2 B' R  F2 U2 L2 F2 D2 R2 D2 F2 R' 
test: LFBLUDUBFLRDRRFRFRBUURFUFBURDFUDRBDDFBRLLBLLDLLDUBDBFU
Find 21 step solution in 82ms: F  R  U' R' D  R  D2 F  D' U2 L  U2 B2 R' D2 R' F2 L  U2 D2 R2 
test: UDDFURBURFFFBRLRUURFURFDBLFLBDDDRDLBFLUBLBBRDLFLDBULUR
Find 22 step solution in 284ms: R2 D' R  L' F' R2 U  D  F  R2 U2 L2 F2 D' L2 F2 U2 B2 D  R2 D  B  
test: LDUBURFBLDUBBRUBLDURBDFLDFURRRLDFLURFDRLLFFUBLRDBBDFFU
Find 21 step solution in 202ms: L' U' B' R' L2 U2 F  L2 F2 U  L2 D  B2 R2 F2 L2 D' B2 U2 B' U' 
test: UFDBUBRRLULLBRRDLFUUFDFDUDFLRLUDDDRDRUBLLFBFBBLFBBURFR
Find 21 step solution in 167ms: B2 D  R' B2 R' U2 R' F2 L  U2 R' D2 F2 R  F  D2 L' U2 L' B2 D' 
test: RRLUUDUUFLRUFRLLFURLURFDRBBDDDDDRLURBBFBLUDLFBBDFBLBFF
Find 18 step solution in 146ms: D' R  B2 U2 B' U2 R2 B2 F' U2 R2 D  L  U' R  B2 R  D2 
test: RFURULBLLFBLURUBUDUDDDFRFLUUFRBDBDDLDDLFLFBRRFRFLBUBBR
Find 21 step solution in 175ms: F  U' B2 R' F' D' B' L' D  R2 D2 F  U2 B  U2 B  R2 B' L2 D2 U' 
test: BRUBUUULLURBRRULDRRDFUFFFRBDDDFDBFLBDUFFLFDDLLBRLBLUBR
Find 20 step solution in 193ms: F2 D' B  D  L' D  R  F2 U2 R2 F2 D2 R2 B2 D2 F2 U' B  R  D  
test: LRBBUFRLRUULFRRLRLBFBBFDUUFRLUDDUFDDDLDULDDRFUFBBBBFLR
Find 18 step solution in 32ms: R  D2 F' B' U  F' U' F' L  B2 D' B2 U2 R2 D  B2 L2 U' 
test: DLRDUDDUULFUBRRLBRLFBRFRFLBRUDBDLLDBRBFDLFFUDFFBUBLURU
Find 20 step solution in 134ms: B2 D2 U2 R2 F2 R' B2 D2 L' R2 D2 F  L  D2 U' B  F' D' F' R' 
test: FBUBUFRLLDDRLRDDUBDFBDFUBUFDFLFDBFULULFDLRURRBRRBBLURL
Find 20 step solution in 100ms: R  L  F' R  D' F  B2 D  L  F  U2 R2 U' D2 F2 U' F2 B2 L2 D' 
test: FFFBUULDBRFRLRFFRUDBULFUBUUDBLRDDFDBDLBRLDDURULLRBBLFR
Find 20 step solution in 128ms: F2 D2 L2 R' B2 L' U2 R  B2 U2 F2 D  R  D  F' R  D' B2 F' U' 
test: UUBFUDLRBURDRRLRFFUULLFFDLURBFBDDDFLBUFDLDRRBLBRUBBDLF
Find 21 step solution in 111ms: F  L' B2 R2 U  R2 L  D2 B' R' F2 D2 L  F2 R2 U2 R' D2 L  U2 B2 
test: LLDBUFUBRFDFFRUBBRFLUBFRDLURURUDUBRFDRLLLDLRBLDBFBFDDU
Find 19 step solution in 157ms: B' D  L2 D2 B2 R  U  D2 L' D2 B2 R2 B' L2 B' R2 D2 F  B2 
test: DFDLURBLBRBRFRUFLLUDUUFRBDRDFUBDFLUBLBLRLBFDRFUFRBDDLU
Find 21 step solution in 113ms: D' R' F  L2 R2 D2 B  L2 B2 F' R2 D2 B2 D2 L' B' D' R' F' U  L' 
test: LBULUBULLBRFDRDFUBBDUUFBDFDRRRBDFFDDFFRULRULBRUDFBLLRL
Find 20 step solution in 92ms: U2 R' B2 U2 B' R  L  U  F' R2 U  R2 F2 U2 B2 D  F2 U' D  B2 
test: FRURULRDLUFBDRBDUUDBFUFLDLLLUBLDRBRRUBFDLFRBFLFRUBFBDD
Find 20 step solution in 64ms: F2 L2 R2 D  F2 D  R2 B2 R2 B2 D' U2 L  R2 B  D' F  U' B2 L2 
test: DRBFUULLUBFLRRLUBDDURBFURBLDUFDDDFFFRRBRLLRFFUBBDBDLLU
Find 20 step solution in 93ms: U2 B' U  R  U  B  U2 D' R' B2 L2 F2 U  D2 R2 D  R2 D' F2 D' 
test: BFFDURBDBDFLBRRLDFRLRUFLDUFBBULDBRDDUFURLLUFLDULBBURRF
Find 20 step solution in 33ms: U' R' D' F  R2 L' F' B' U2 R  B2 L' D2 R  B2 D2 R  U2 L' U2 
test: UBRUUBUFFRDURRBDULFDDDFFLUBDBRLDRUDDLFLLLRRFBFRBLBUFLB
Find 21 step solution in 95ms: R2 D2 B2 D' L2 U  L2 F2 U' B2 D' U' L  D  L2 B  U2 R' F  U' L2 
test: FFLLUFLDURDDRRLDRLUBFRFUULBBBRFDDDFURUFBLBLURFLDDBUBRB
Find 22 step solution in 301ms: L' U2 R2 D' R2 F  L  U' F' U  F2 U2 R  D2 L2 B2 L  F2 L  U2 R' D2 
test: LLURUURFDFBLRRDUBFURRBFURRFBBRDDDLLLDDBFLLULDFFBFBUDUB
Find 20 step solution in 69ms: F2 B2 D  B2 U  F2 L  B' U  R  U2 L2 D2 F2 R  U2 R  F2 B2 D2 
test: BFBRUURDDFRDFRBBUUFBRDFLLRLFFUUDFFURDDUBLLULDLDRRBLBBL
Find 20 step solution in 172ms: U  B' U' B  U2 R  U  D' L  F' B2 D' B2 R2 U  B2 R2 U' D2 B2 
test: BDDUUDDFRFRFFRFRLRRRULFLDRFBBDUDBFBBURBULDULLLFLUBBUDL
Find 21 step solution in 160ms: R' F2 D2 B2 D  R2 F2 D  B2 U2 B2 L2 U  R' U' L2 B' L' B2 L' B' 
test: UBURUUBUURLBFRURDLDBFFFDRLBDBUBDLBFDFFRDLUDDFLRLRBRFLL
Find 22 step solution in 216ms: U  F' D' F' B  U2 R  B2 D  L  D' L2 F2 U  B2 U' L2 U2 F2 D  L2 U' 
test: BDBRULULUBUDFRUDRFLFRUFRULRRDFFDBLBUDDBBLBDUFLFRRBLLDF
Find 21 step solution in 109ms: U  B' U' B2 R  L  B' U2 B2 U  L2 F2 U' L2 U2 B2 D  L2 U2 F' U' 
test: FUFLUFRUBUDLFRRBLBFRLBFLLRUDDRUDDUBRRBUFLRLLBDBDFBUDDF
Find 20 step solution in 85ms: L  U' L2 U2 B  R' F2 U' R2 U  B2 U  B2 U2 L2 F2 B2 U  L  F' 
test: URRLULRRULFFURRRDLFDBUFLLBDFDBFDLBFBFBURLBUUDDFLUBBDDR
Find 22 step solution in 134ms: F  B2 U' R  D' L' B' D' L  F  U2 B2 U  F2 R2 U  R2 F2 U2 F2 U2 L2 
totel time cost 6424ms
stepper_zero: 699, 1490, 283
tcs3472_check_id(0) pass
tcs3472_check_id(1) pass

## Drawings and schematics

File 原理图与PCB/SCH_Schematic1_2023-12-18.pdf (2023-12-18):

RP2040

## Raspberry Pi

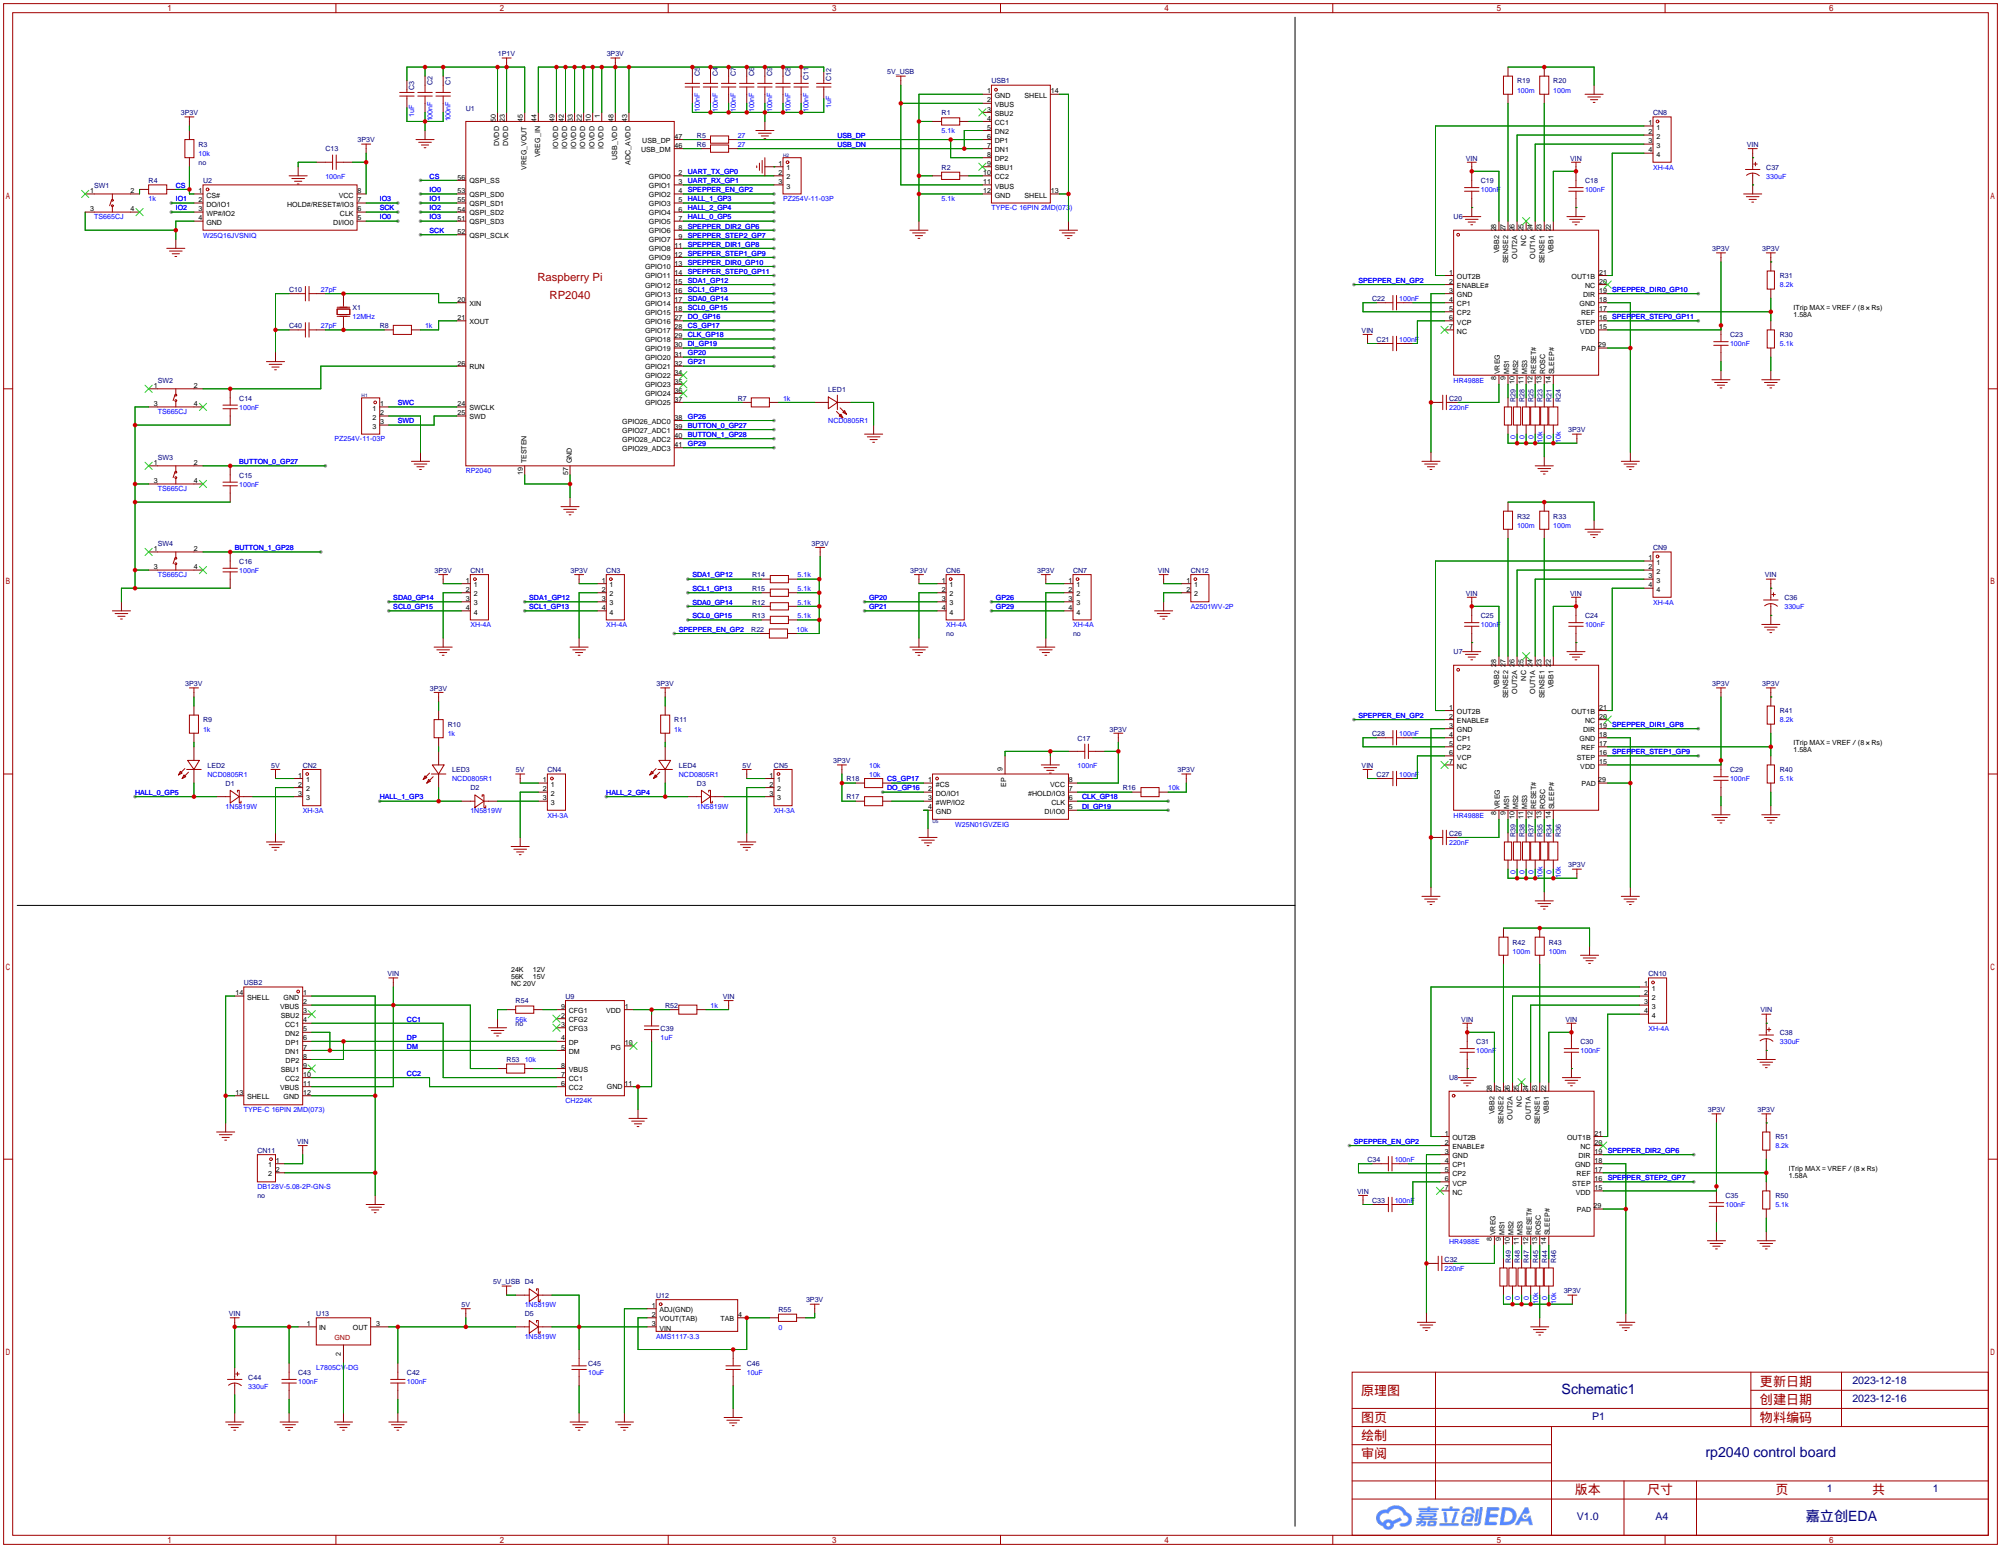
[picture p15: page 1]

ITrip MAX＝VREF／(8 Rs)

DP
DM

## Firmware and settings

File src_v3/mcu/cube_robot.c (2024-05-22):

#include <stdio.h>
#include <math.h>
#include <string.h>
#include "pico/stdlib.h"
#include "hardware/pio.h"
#include "hardware/clocks.h"
#include "hardware/irq.h"
#include "step_ctrl.pio.h"
#include "color_detect.h"
#include "solve.h"

// 步进电机使能信号 低有效 (20220706 由16改为2)
#define SPEPPER_EN    2  
// 步进电机控制信号
#define SPEPPER_STEP0 11
#define SPEPPER_DIR0  10
#define SPEPPER_STEP1 9
#define SPEPPER_DIR1  8
#define SPEPPER_STEP2 7
#define SPEPPER_DIR2  6
// 霍尔开关,用于寻找零点
#define HALL_0        5
#define HALL_1        3
#define HALL_2        4
// 按键(20220710 由0,1改为27,28)
#define BUTTON_0      27
#define BUTTON_1      28
#define LED_PIN PICO_DEFAULT_LED_PIN

// 颜色传感器信号{{SDA,SCL},{SDA,SCL}}
const uint i2c_gpio[2][2] = {{14,15}, {12,13}};

// 根据实际测试结果调整电机初始角度
#define STEPPER0_OFFSET 100
#define STEPPER1_OFFSET 110
#define STEPPER2_OFFSET 375

// 顺时针、逆时针的定义,取决与驱动芯片的类型和电机的接线顺序
#define DIR0_CCW false
#define DIR0_CW  true
#define DIR1_CCW false
#define DIR1_CW  true
#define DIR2_CCW true
#define DIR2_CW  false

#define RPM       (200.0f * 16 / 60)

typedef struct step_ctrl_t{
    int s;    // 加速过程需要的步数
    int i;    // 当前步
    int steps;// 步数
    float vi; // 当前速度
    float a;  // 加速度（脉冲/s2）
} step_ctrl;

// MCU的栈较小,因此比较大的数组,放在堆上,防止栈溢出
// cube_robot的全局变量：
uint16_t color_buffer[54*3] = {0}; 
char cube_str[55] = {0};
char solution_str[128] = {0};
step_ctrl stepper_ctrl[3] = {0};
float speed_factor = 1.0f;
float accel_factor = 1.0f;

void sample_color(uint32_t g, uint16_t *buffer);

// 按键处理程序
volatile int button_status[2] = {0,0};
void button_callback(uint gpio, uint32_t events) 
{
    int button_id;
    static absolute_time_t button_fail_time[2] = {0,0};

    if(BUTTON_0 == gpio){
        button_id = 0;
    }else if(BUTTON_1 == gpio){
        button_id = 1;
    }else{
        return;
    }
    if(events == GPIO_IRQ_EDGE_RISE){
        int time_diff = (int)absolute_time_diff_us(button_fail_time[button_id], get_absolute_time()) / 1000;
        if(time_diff <= 20){
            return;
        }else{
            button_status[button_id] = time_diff;
        }
    }
    button_fail_time[button_id] = get_absolute_time();
};
bool button_break(void)
{
    if(button_status[0] || button_status[1]){
        button_status[0] = 0;
        button_status[1] = 0;
        return true;
    }else{
        return false;
    }
}

// -------------------------------------电机控制------------------------------------------------

// 开始电机控制
// sm电机号0-2 steps：步数,v0：初始速度（脉冲/s）,v：最高速度（脉冲/s）,a：加速度（脉冲/s2）
static void stepper_move_none_block(int sm, int steps, float v0, float v, float a)
{
    step_ctrl *p_step_ctrl = &stepper_ctrl[sm];
    p_step_ctrl -> vi = v0 * speed_factor;
    p_step_ctrl -> a = a * accel_factor;
    p_step_ctrl -> s = (int)roundf((v * v - v0 * v0) / (2 * a)); // 计算加速过程需要的步数
    p_step_ctrl -> i = 0;
    p_step_ctrl -> steps = steps;
    pio_set_irq0_source_enabled(pio0, PIO_INTR_SM0_TXNFULL_LSB + sm, true);
}
// 等待电机控制指令执行完毕
static void stepper_move_wait_all(int sm)
{
    // 等待中断关闭
    while(pio0->inte0 & (1u << (sm + PIO_INTR_SM0_TXNFULL_LSB))){
        asm("nop");
    }
    // 等待fifo清空
    while(!pio_sm_is_tx_fifo_empty(pio0, sm)){
        asm("nop");
    }
}
static void stepper_move(int sm, int steps, float v0, float v, float a)
{
    stepper_move_none_block(sm, steps, v0, v, a);
    stepper_move_wait_all(sm);
}
// 等待到输出指定的步数,因为有fifo,所以会提前4个脉冲返回
static void stepper_move_wait(int sm, int step_to_wait)
{
    volatile int *index = &stepper_ctrl[sm].i;
    while(*index <= step_to_wait){
        asm("nop");
    }
}
static void stepper_move_01_with_color_cmd(int steps, const uint32_t *color_cmd, uint16_t *buffer)
{
    const float V_START_WITH_LOAD = 190.0f*RPM;// 带载起跳速度
    const float V_MAX_WITH_LOAD = 380.0f*RPM;  // 带载最大速度
    const float A_MAX_WITH_LOAD = 5.0e5f;      // 带载最大加速度
    // 采样延后量,解决速度快了采样不准确问题,在低速运行不出错的前提下,读取越晚越好
    // 120可能出错 100不出错
    const int SAMPLE_OFFSET = 70;              
    stepper_move_none_block(0, steps, V_START_WITH_LOAD, V_MAX_WITH_LOAD, A_MAX_WITH_LOAD); 
    stepper_move_none_block(1, steps, V_START_WITH_LOAD, V_MAX_WITH_LOAD, A_MAX_WITH_LOAD); 
    // 当 steps = 2400 时
    // 在0 400 800 1200 1600 2000 2400采集
    if(color_cmd != 0){
        for(int i=0; i<steps; i+=400){
            if(color_cmd[i/400] != 0){
                stepper_move_wait(0, i + SAMPLE_OFFSET);
                sample_color(color_cmd[i/400], buffer);
            }
        }
    }
    stepper_move_wait_all(0);
    sleep_us(1200);
    if(color_cmd != 0 && color_cmd[steps/400] != 0){
        sample_color(color_cmd[steps/400], buffer);
    }
}
// 计算脉冲延时
static uint32_t stepper_move_calc(step_ctrl *p_step_ctrl)
{
    const float F = 10000000.0f; // PIO频率
    float accel;
    int i = p_step_ctrl -> i;
    int s = p_step_ctrl -> s;
    int steps = p_step_ctrl -> steps;
    float vi = p_step_ctrl -> vi;
    float a = p_step_ctrl -> a;
    if (i < s && i < steps / 2){
        accel = a;
    }else if (i >= steps - s){
        accel = -a;
    }else{
        accel = 0;
    }
    vi = sqrtf(vi * vi + 2.0f * accel);
    p_step_ctrl -> vi = vi;
    p_step_ctrl -> i = i + 1;
    return (uint32_t)roundf(F / vi) - 33; // 33的来源参考step_ctrl.pio
}
// PIO FIFO非满中断,每次处理耗时5us左右
void pio_fifo_not_full_handler()
{
    //gpio_put(PICO_DEFAULT_LED_PIN, 1);
    step_ctrl *p;
    uint32_t date;
    int sm;
    // 对应通道中断功能开启,且FIFO非满,此时应当填充新的数据
    for(sm=0;sm<3;sm++){
        while((pio0->inte0 & (1u << (sm + PIO_INTR_SM0_TXNFULL_LSB))) && !pio_sm_is_tx_fifo_full(pio0, sm)){
            p = &stepper_ctrl[sm];
            date = stepper_move_calc(p);
            pio_sm_put(pio0, sm, date);
            if (p->i >= p->steps) {
                pio_set_irq0_source_enabled(pio0, sm + PIO_INTR_SM0_TXNFULL_LSB, false);
                break;
            }
        }
    }
    //gpio_put(PICO_DEFAULT_LED_PIN, 0);
}
// 初始化电机控制PIO
static void init_stepper_ctrl(void)
{
    // 初始化PIO
    uint offset = pio_add_program(pio0, &step_ctrl_program);
    step_ctrl_program_init(pio0, 0, offset, SPEPPER_STEP0);
    step_ctrl_program_init(pio0, 1, offset, SPEPPER_STEP1);
    step_ctrl_program_init(pio0, 2, offset, SPEPPER_STEP2);
    // 开中断
    irq_set_exclusive_handler(PIO0_IRQ_0, pio_fifo_not_full_handler);
    irq_set_enabled(PIO0_IRQ_0, true);
}

// 电机移动归零
void stepper_zero(void) 
{
    bool s0,s1,s2;
    int i = 0, j = 0, k = 0;
    bool s0_ok = false;
    bool s1_ok = false;
    bool s2_ok = false;
    s0 = gpio_get(HALL_0);
    s1 = gpio_get(HALL_1);
    s2 = gpio_get(HALL_2);
    while (!(s0_ok && s1_ok && s2_ok))
    {
        if(s0_ok == false){
            gpio_put(SPEPPER_STEP0, 1);
            sleep_us(4);
            i++;
            gpio_put(SPEPPER_STEP0, 0);
            if(!s0 && gpio_get(HALL_0))
                s0_ok = true;
            s0 = gpio_get(HALL_0);
        }
        if(s1_ok == false){
            gpio_put(SPEPPER_STEP1, 1);
            sleep_us(4);
            j++;
            gpio_put(SPEPPER_STEP1, 0);
            if(!s1 && gpio_get(HALL_1))
                s1_ok = true;
            s1 = gpio_get(HALL_1);
        }
        if(s2_ok == false){
            gpio_put(SPEPPER_STEP2, 1);
            sleep_us(4);
            k++;
            gpio_put(SPEPPER_STEP2, 0);
            if(!s2 && gpio_get(HALL_2))
                s2_ok = true;
            s2 = gpio_get(HALL_2);
        }
        sleep_us(400);
    }
    printf("stepper_zero: %d, %d, %d\n",i,j,k);
}
// IO初始化
void init_io(void)
{
    gpio_init(LED_PIN);
    gpio_init(SPEPPER_EN);
    gpio_init(SPEPPER_DIR0);
    gpio_init(SPEPPER_DIR1);
    gpio_init(SPEPPER_DIR2);
    gpio_init(SPEPPER_STEP0);
    gpio_init(SPEPPER_STEP1);
    gpio_init(SPEPPER_STEP2);
    gpio_init(SPEPPER_STEP2);
    gpio_init(HALL_0);
    gpio_init(HALL_1);
    gpio_init(HALL_2);
    gpio_init(BUTTON_0);
    gpio_init(BUTTON_1);

    gpio_put(SPEPPER_EN,    1);
    gpio_put(SPEPPER_DIR0,  0);
    gpio_put(SPEPPER_DIR1,  0);
    gpio_put(SPEPPER_DIR2,  0);
    gpio_put(SPEPPER_STEP0, 0);
    gpio_put(SPEPPER_STEP1, 0);
    gpio_put(SPEPPER_STEP2, 0);

    gpio_set_dir(LED_PIN, GPIO_OUT);
    gpio_set_dir(SPEPPER_EN, GPIO_OUT);
    gpio_set_dir(SPEPPER_DIR0, GPIO_OUT);
    gpio_set_dir(SPEPPER_DIR1, GPIO_OUT);
    gpio_set_dir(SPEPPER_DIR2, GPIO_OUT);
    gpio_set_dir(SPEPPER_STEP0, GPIO_OUT);
    gpio_set_dir(SPEPPER_STEP1, GPIO_OUT);
    gpio_set_dir(SPEPPER_STEP2, GPIO_OUT);

    gpio_set_dir(HALL_0, GPIO_IN);
    gpio_set_dir(HALL_1, GPIO_IN);
    gpio_set_dir(HALL_2, GPIO_IN);
    gpio_set_dir(BUTTON_0, GPIO_IN);
    gpio_set_dir(BUTTON_1, GPIO_IN);

    gpio_pull_up(HALL_0);
    gpio_pull_up(HALL_1);
    gpio_pull_up(HALL_2);
    gpio_pull_up(BUTTON_0);
    gpio_pull_up(BUTTON_1);

    for (int i=0;i<2;i++){
        for(int j=0;j<2;j++){
            gpio_init(i2c_gpio[i][j]);
            gpio_pull_up(i2c_gpio[i][j]);
            gpio_set_dir(i2c_gpio[i][j], GPIO_IN);
            gpio_put(i2c_gpio[i][j], 0);
        }
    }
}
// --------------- 魔方控制部分 -----------------------
// 旋转魔方的上下(U D)面,注意参数只支持正数,U为逆时针,D为顺时针
// 参数取值范围0 800 1600 2400,不可以同时为0
// U 黄色 0号电机
// D 白色 1号电机
// 支持合并操作,可以同时旋转U和D
void cube_ud(int face_u, int face_d)
{
    const int gap = 24;
    const float V_START_WITH_LOAD = 150.0f*RPM; // 带载起跳速度
    const float V_MAX_WITH_LOAD = 500.0f*RPM;  // 带载最大速度
    const float A_MAX_WITH_LOAD = 4.5e5f;       // 带载最大加速度
    // const float V_START_GAP = 100.0f*RPM;    // 卡住魔方中间层时的运行速度
    gpio_put(SPEPPER_DIR0, DIR0_CCW);
    gpio_put(SPEPPER_DIR1, DIR1_CW);
    // 步骤1：卡住魔方中间层(V20版本框架更加坚固,不需要这个操作)
    //stepper_move_none_block(0, gap, V_START_GAP, V_MAX_WITH_LOAD, A_MAX_WITH_LOAD);
    //stepper_move           (1, gap, V_START_GAP, V_MAX_WITH_LOAD, A_MAX_WITH_LOAD);
    // 步骤2：旋转需要的角度
    if(face_u > 0){
        stepper_move_none_block(0, face_u, V_START_WITH_LOAD, V_MAX_WITH_LOAD, A_MAX_WITH_LOAD);
    }
    if(face_d > 0){
        stepper_move_none_block(1, face_d, V_START_WITH_LOAD, V_MAX_WITH_LOAD, A_MAX_WITH_LOAD);
    }
    if(face_u > face_d){
        stepper_move_wait_all(0);
    }else{
        stepper_move_wait_all(1);
    }
    // 步骤3：恢复初始位置(V20版本框架更加坚固,不需要这个操作)
    //sleep_ms(1);
    //gpio_put(SPEPPER_DIR0, DIR0_CW);
    //gpio_put(SPEPPER_DIR1, DIR1_CCW);
    //stepper_move_none_block(0, gap, V_START_GAP, V_MAX_WITH_LOAD, A_MAX_WITH_LOAD);
    //stepper_move           (1, gap, V_START_GAP, V_MAX_WITH_LOAD, A_MAX_WITH_LOAD);
    sleep_us(1600);
}
// 旋转魔方的左前右后面(L F R B),参数正负都可以,正数表示顺时针,负数表示逆时针
// 参数取值范围 800 1600 -800 -1600
void cube_lfrb(int steps)
{
    const float V_START_NO_LOAD = 170.0f*RPM;   // 空载起跳速度
    const float V_MAX_NO_LOAD = 1500.0f*RPM;    // 空载最大速度 1500RPM = 80KHz
    const float A_MAX_NO_LOAD = 15e5f;          // 空载最大加速度
    const float V_START_WITH_LOAD = 170.0f*RPM; // 带载起跳速度
    const float V_MAX_WITH_LOAD = 600.0f*RPM;  // 带载最大速度
    const float A_MAX_WITH_LOAD = 5.5e5f;       // 带载最大加速度
    const float V_SLOW = 120.0f*RPM; // 最后一小段要低速运转,等待魔方减速
    const int TOUCH_STEP = 256;
    const int SLOW_STEP = 100;
    bool dir;
    if(steps > 0){
        dir = DIR2_CW;
    }else{
        dir = DIR2_CCW;
        steps = -steps;
    }
    // 步骤1：旋转臂接触魔方,接触之前应当减速,否则接触后受力突变,会丢步
    gpio_put(SPEPPER_DIR2, dir);
    stepper_move(2, TOUCH_STEP, V_START_NO_LOAD, V_MAX_NO_LOAD, A_MAX_NO_LOAD);
    // 步骤2：旋转需要的角度
    stepper_move(2, steps - SLOW_STEP, V_START_WITH_LOAD, V_MAX_NO_LOAD, A_MAX_WITH_LOAD);
    // 步骤3：最后一小段要低速运转
    stepper_move(2, SLOW_STEP, V_SLOW, V_SLOW, A_MAX_WITH_LOAD);
    // 步骤4：恢复初始位置
    sleep_us(1200);
    gpio_put(SPEPPER_DIR2, !dir);
    stepper_move(2, TOUCH_STEP, V_START_NO_LOAD, V_MAX_NO_LOAD, A_MAX_NO_LOAD);
}

// 翻转魔方,参数只能为正
// 参数取值范围 800 1600 2400
// 翻转魔方时,动力来自两个电机,可以设置较高的速度
void flip_cube(int steps)
{
    const float V_START_WITH_LOAD = 190.0f*RPM;// 带载起跳速度
    const float V_MAX_WITH_LOAD = 500.0f*RPM;  // 带载最大速度
    const float A_MAX_WITH_LOAD = 5.0e5f;      // 带载最大加速度
    gpio_put(SPEPPER_DIR0, DIR0_CW);
    gpio_put(SPEPPER_DIR1, DIR1_CCW);
    stepper_move_none_block(0, steps, V_START_WITH_LOAD, V_MAX_WITH_LOAD, A_MAX_WITH_LOAD);
    stepper_move           (1, steps, V_START_WITH_LOAD, V_MAX_WITH_LOAD, A_MAX_WITH_LOAD);
    sleep_us(2000);
}
// 采集颜色
int cube_get_color(uint16_t *buffer)
{
    #define UD(x,y) ( ((x)<<8) | (y) )
    const uint32_t color_cmd_0_270_L[7] = {UD(36,42),UD(23,48),UD(38,44),UD(10,43),UD(9,15),UD(50,21),UD(11,17)};
    const uint32_t color_cmd_1_180_R[5] = {0,UD(37,16),UD(33,27),UD(19,52),UD(0,6)};
    const uint32_t color_cmd_2_270_F[7] = {0,0,UD(29,35),UD(46,25),UD(8,2),0,0};
    const uint32_t color_cmd_3_180_B[5] = {0,0,UD(18,51),UD(12,41),UD(47,26)};
    const uint32_t color_cmd_4_270_R[7] = {0,0,UD(45,24),UD(39,14),UD(20,53),0,0};
    const uint32_t color_cmd_5_180_L[5] = {0,0,0,UD(5,32),0};
    //const uint32_t color_cmd_6_90_F[3]= {0,0,0};
    const uint32_t color_cmd_7_180_B[5] = {0,UD(3,30),0,UD(7,28),0};
    const uint32_t color_cmd_8_180  [5] = {0,0,0,UD(1,34),0};

    gpio_put(SPEPPER_DIR0, DIR0_CW);
    gpio_put(SPEPPER_DIR1, DIR1_CCW);
    stepper_move_01_with_color_cmd(2400, color_cmd_0_270_L, buffer); 
    if(button_break())return 1;
    cube_lfrb(800);
    if(button_break())return 1;
    stepper_move_01_with_color_cmd(1600, color_cmd_1_180_R, buffer); 
    if(button_break())return 1;
    cube_lfrb(800);
    if(button_break())return 1;
    stepper_move_01_with_color_cmd(2400, color_cmd_2_270_F, buffer); 
    if(button_break())return 1;
    cube_lfrb(800);
    if(button_break())return 1;
    stepper_move_01_with_color_cmd(1600, color_cmd_3_180_B, buffer); 
    if(button_break())return 1;
    cube_lfrb(800);
    if(button_break())return 1;
    stepper_move_01_with_color_cmd(2400, color_cmd_4_270_R, buffer); 
    if(button_break())return 1;
    cube_lfrb(800);
    if(button_break())return 1;
    stepper_move_01_with_color_cmd(1600, color_cmd_5_180_L, buffer); 
    if(button_break())return 1;
    cube_lfrb(800);
    if(button_break())return 1;
    stepper_move_01_with_color_cmd(800 , 0                , buffer); 
    if(button_break())return 1;
    cube_lfrb(800);
    if(button_break())return 1;
    stepper_move_01_with_color_cmd(1600, color_cmd_7_180_B, buffer); 
    if(button_break())return 1;
    cube_lfrb(800);
    if(button_break())return 1;
    stepper_move_01_with_color_cmd(1600, color_cmd_8_180  , buffer);
    return 0;
}
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
int main(void)
{
    stdio_init_all();    
    init_io();
    sleep_ms(100);
    if(!gpio_get(BUTTON_0) || !gpio_get(BUTTON_1)){
        // 启动时等待USB建立链接，方便看到调试信息
        sleep_ms(5000);
        printf("Init.\n");
        // 性能测试
        debug_solve();
    }
    // 步进电机回零
    gpio_put(SPEPPER_EN, 0);
    stepper_zero();
    // 在此之后,使用PIO控制电机
    init_stepper_ctrl();
    stepper_move_none_block(0, STEPPER0_OFFSET, 100*RPM,300*RPM,150000);
    stepper_move_none_block(1, STEPPER1_OFFSET, 100*RPM,300*RPM,150000);
    stepper_move_none_block(2, STEPPER2_OFFSET, 100*RPM,300*RPM,150000);
    // 检查颜色传感器是否正常,并且初始化
    for(int i=0; i<2; i++){
        if(tcs3472_check_id(i)){
            tcs3472_enable(i);
            printf("tcs3472_check_id(%d) pass\n",i);
        }else{
            printf("tcs3472_check_id(%d) fail\n",i);
            while (1);            
        }
    }
    // 初始化按键中断
    gpio_set_irq_enabled_with_callback(BUTTON_0, GPIO_IRQ_EDGE_FALL | GPIO_IRQ_EDGE_RISE, true, &button_callback);
    gpio_set_irq_enabled_with_callback(BUTTON_1, GPIO_IRQ_EDGE_FALL | GPIO_IRQ_EDGE_RISE, true, &button_callback);
    bool auto_test = false;
    int scramble_index = 0;
    char face = 'F';
    while (1) 
    {
        // 等待按键按下
        while(!auto_test)
        {
            if(button_status[1]){
                printf("button 1 press %d ms.\n", button_status[1]);
                if(button_status[1] < 500){
                    // 按下时间小于0.5s
                    speed_factor = 1.0f;
                    accel_factor = 1.0f;
                }else{
                    // 按下时间大于等于0.5s
                    speed_factor = 0.125f;// 降速设置
                    accel_factor = 0.125f * 0.125f;
                }
                button_status[1] = 0;
                auto_test = false;
                break;
            }

            if(button_status[0]){
                printf("button 0 press %d ms.\n", button_status[0]);
                if(button_status[0] < 500){
                    // 按下时间小于0.5s
                    speed_factor = 1.0f;
                    accel_factor = 1.0f;
                }else{
                    // 按下时间大于等于0.5s
                    speed_factor = 0.125f;// 降速设置
                    accel_factor = 0.125f * 0.125f;
                }
                auto_test = true;
                scramble_index = 0;
                button_status[0] = 0;
                break;
            }
        }

        // 打乱魔方
        if(auto_test){
            face = 'F';
            printf("test case %d, ",scramble_index);
            absolute_time_t tt1 = get_absolute_time();
            strcpy(solution_str, scramble_string[scramble_index]);
            face = cube_tweak_str(face, solution_str);
            if(face == 0){
                printf("stop cube_tweak_str.\n");
                auto_test = false;
                continue;
            }
            absolute_time_t tt2 = get_absolute_time();
            printf("Scramble time cost: %dms\n", (int)absolute_time_diff_us(tt1, tt2) / 1000);
            face = cube_tweak(face, "F0", 0);// 完成后,调整魔方朝向
            sleep_ms(500);
        }
        // 采集每一块的颜色
        absolute_time_t t1,t2,t3,t4;
        t1 = get_absolute_time();
        if(cube_get_color(color_buffer) == 1)
        {
            printf("stop cube_get_color.\n");
            auto_test = false;
            continue;
        }
        // 识别颜色
        color_detect(color_buffer, cube_str);
        for(int i=0; i<54*3; i++){
            // 用完清理数据,这很重要,这BUG调了一小时
            // 魔方中间块对应的6个数据,每次重新采样是不会更新的
            color_buffer[i] = 0;
        }
        if(cube_str[0] != 'E' ){
            printf("%s,", cube_str);
        }else{
            printf("Error,%s,", cube_str);
        }
        t2 = get_absolute_time();
        printf("%dms,", (int)absolute_time_diff_us(t1, t2) / 1000);
        // 求解魔方
        char *solution;
        if(cube_str[0] != 'E'){
            int steps = solve(cube_str, solution_str);
            if(steps >= 0){
                printf("%s(%d steps),", solution_str, steps);
                solution = solution_str;
            }else{
                printf("Cube Error,");
                solution = 0;
            }
        }else{
            printf("Color Error,");
            solution = 0;
        }
        t3 = get_absolute_time();
        printf("%dms,", (int)absolute_time_diff_us(t2, t3) / 1000);
        // 计算完成后执行对应的动作
        face = 'F';
        if(solution != 0 && solution[0] != 0){
            face = cube_tweak_str(face, solution);
            if(face == 0){
                printf("stop cube_tweak_str.\n");
                auto_test = false;
                continue;
            }
        }
        t4 = get_absolute_time();
        printf("%dms,", (int)absolute_time_diff_us(t3, t4) / 1000);
        printf("%dms\n", (int)absolute_time_diff_us(t1, t4) / 1000);
        if(auto_test){
            face = cube_tweak(face, "F0", 0);// 完成后,调整魔方朝向
            sleep_ms(500);
            scramble_index++;
            if(scramble_index >= scramble_count){
                scramble_index = 0;
                auto_test = false;
            }
        }
    }
    return 0;
}

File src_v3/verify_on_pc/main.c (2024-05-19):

#include <stdio.h>
#include <assert.h>
#include <inttypes.h>
#include <string.h>
#include <fcntl.h>
#include <unistd.h>
#include <stdlib.h>
#include <time.h>  
#include "solve.h"

typedef enum route_enum {
    L=0, L3, L2, R, R3, R2, U, U3, U2, D, D3, D2, F, F3, F2, B, B3, B2
}route_t;

typedef struct cube_struct{
    uint8_t ep[12];
    uint8_t er[12];
    uint8_t cp[8];
    uint8_t cr[8];
} cube_t;

// 用于转换两种表示方式 20个棱块角块 <---> 54个面
// [UF, UR, UB, UL,DF, DR, DB, DL, FR, FL, BR, BL] [UFR, URB, UBL, ULF, DRF, DFL, DLB, DBR]
// UUUUUUUUURRRRRRRRRFFFFFFFFFDDDDDDDDDLLLLLLLLLBBBBBBBBB
static const char edge_to_face[12][2] = {
    {7, 19},  {5, 10},  {1, 46},  {3, 37},
    {28, 25}, {32, 16}, {34, 52}, {30, 43},
    {23, 12}, {21, 41}, {48, 14}, {50, 39}
};
static const char corner_to_face[8][3] = {
    {8, 20, 9}, {2, 11, 45}, {0, 47, 36}, {6, 38, 18},
    {29, 15, 26}, {27, 24, 44}, {33, 42, 53}, {35, 51, 17}
};
static const char edge_index[24][2] = {
    "UF","UR","UB","UL","DF","DR","DB","DL","FR","FL","BR","BL",
    "FU","RU","BU","LU","FD","RD","BD","LD","RF","LF","RB","LB"
};
static const char corner_index[24][3] = {
    "UFR","URB","UBL","ULF","DRF","DFL","DLB","DBR",
    "FRU","RBU","BLU","LFU","RFD","FLD","LBD","BRD",
    "RUF","BUR","LUB","FUL","FDR","LDF","BDL","RDB"
};
// 54个面的表示方式，转换为棱块角块表示方式
// 正常 返回1 错误 返回0
static int cube_from_face_54(cube_t *c, const char *cube_str)
{
    int sum = 0;
    // 棱块
    for(int i=0; i<12; i++){
        int index_a = edge_to_face[i][0];
        int index_b = edge_to_face[i][1];
        int tmp;
        for(tmp=0;tmp<24;tmp++){
            if( edge_index[tmp][0] == cube_str[index_a] &&
                edge_index[tmp][1] == cube_str[index_b] ){
                break;
            }
        }
        if(tmp < 24){
            c -> ep[i] = tmp % 12;
            c -> er[i] = tmp / 12;
        }else{
            printf("Error: invalid edge %c%c.\n",
                   cube_str[index_a],cube_str[index_b]);
            return 0;
        }
    }
    for(int i=0; i<12; i++){
        for(int j=0; j<12; j++){
            if(i != j && c -> ep[i] == c -> ep[j]){
                printf("Error: repetition edge.\n");
                return 0;
            }
        }
    }
    sum = 0;
    for(int i=0; i<12; i++){
        sum += c -> er[i];
    }
    if(sum%2 != 0){
        // 单个棱块翻转，不影响后续程序运行
        // 测试用例BRBBUUFLFUFULRLDDBLBRDFULBRFRFFDBBLRUUURLRDDDRFLDBUDFL
        printf("Flipped edge, ignore.\n");
    }
    // 角块
    for(int i=0; i<8; i++){
        int index_a = corner_to_face[i][0];
        int index_b = corner_to_face[i][1];
        int index_c = corner_to_face[i][2];
        int tmp;
        for(tmp=0;tmp<24;tmp++){
            if( corner_index[tmp][0] == cube_str[index_a] &&
                corner_index[tmp][1] == cube_str[index_b] &&
                corner_index[tmp][2] == cube_str[index_c]){
                break;
            }
        }
        if(tmp < 24){
            c -> cp[i] = tmp % 8;
            c -> cr[i] = tmp / 8;
        }else{
            printf("Error: invalid corner %c%c%c.\n",
                   cube_str[index_a],cube_str[index_b],cube_str[index_c]);
            return 0;
        }
    }
    for(int i=0; i<8; i++){
        for(int j=0; j<8; j++){
            if(i != j && c -> cp[i] == c -> cp[j]){
                printf("Error: repetition corner.\n");
                return 0;
            }
        }
    }
    sum = 0;
    for(int i=0; i<8; i++){
        sum += c -> cr[i];
    }
    if(sum%3 != 0){
        // 单个角块旋转，不影响后续程序运行
        printf("Twisted corner, ignore.\n");
    }
    // 校验棱块和角块之间的位置关系
    int cornerParity = 0;
    for (int i = 7; i >= 1; i--)
        for (int j = i - 1; j >= 0; j--)
            if (c->cp[j] > c->cp[i])
                cornerParity++;
    cornerParity = cornerParity % 2;
    int edgeParity = 0;
    for (int i = 11; i >= 1; i--)
        for (int j = i - 1; j >= 0; j--)
            if (c->ep[j] > c->ep[i])
                edgeParity++;
    edgeParity = edgeParity % 2;
    if ((edgeParity ^ cornerParity) != 0) {
        printf("ERROR: parity error.\n");
        return 0;
    }
    return 1;
}
// 用于验证正确性的测试代码
static const uint8_t route_tab_ep[18][12]={
    {0,1,2,11,4,5,6,9,8,3,10,7},// L  0
    {0,1,2,9,4,5,6,11,8,7,10,3},// L' 1
    {0,1,2,7,4,5,6,3,8,11,10,9},// L2 2
    {0,8,2,3,4,10,6,7,5,9,1,11},// R  3
    {0,10,2,3,4,8,6,7,1,9,5,11},// R' 4
    {0,5,2,3,4,1,6,7,10,9,8,11},// R2 5
    {1,2,3,0,4,5,6,7,8,9,10,11},// U  6
    {3,0,1,2,4,5,6,7,8,9,10,11},// U' 7
    {2,3,0,1,4,5,6,7,8,9,10,11},// U2 8
    {0,1,2,3,7,4,5,6,8,9,10,11},// D  9
    {0,1,2,3,5,6,7,4,8,9,10,11},// D' 10
    {0,1,2,3,6,7,4,5,8,9,10,11},// D2 11
    {9,1,2,3,8,5,6,7,0,4,10,11},// F  12
    {8,1,2,3,9,5,6,7,4,0,10,11},// F' 13
    {4,1,2,3,0,5,6,7,9,8,10,11},// F2 14
    {0,1,10,3,4,5,11,7,8,9,6,2},// B  15
    {0,1,11,3,4,5,10,7,8,9,2,6},// B' 16
    {0,1,6,3,4,5,2,7,8,9,11,10} // B2 17
};
static const uint8_t route_tab_er[18][12]={
    {0,0,0,0,0,0,0,0,0,0,0,0},// L  0
    {0,0,0,0,0,0,0,0,0,0,0,0},// L' 1
    {0,0,0,0,0,0,0,0,0,0,0,0},// L2 2
    {0,0,0,0,0,0,0,0,0,0,0,0},// R  3
    {0,0,0,0,0,0,0,0,0,0,0,0},// R' 4
    {0,0,0,0,0,0,0,0,0,0,0,0},// R2 5
    {0,0,0,0,0,0,0,0,0,0,0,0},// U  6
    {0,0,0,0,0,0,0,0,0,0,0,0},// U' 7
    {0,0,0,0,0,0,0,0,0,0,0,0},// U2 8
    {0,0,0,0,0,0,0,0,0,0,0,0},// D  9
    {0,0,0,0,0,0,0,0,0,0,0,0},// D' 10
    {0,0,0,0,0,0,0,0,0,0,0,0},// D2 11
    {1,0,0,0,1,0,0,0,1,1,0,0},// F  12
    {1,0,0,0,1,0,0,0,1,1,0,0},// F' 13
    {0,0,0,0,0,0,0,0,0,0,0,0},// F2 14
    {0,0,1,0,0,0,1,0,0,0,1,1},// B  15
    {0,0,1,0,0,0,1,0,0,0,1,1},// B' 16
    {0,0,0,0,0,0,0,0,0,0,0,0} // B2 17
};
static const uint8_t route_tab_cp[18][8]={
    {0,1,6,2,4,3,5,7},// L  0
    {0,1,3,5,4,6,2,7},// L' 1
    {0,1,5,6,4,2,3,7},// L2 2
    {4,0,2,3,7,5,6,1},// R  3
    {1,7,2,3,0,5,6,4},// R' 4
    {7,4,2,3,1,5,6,0},// R2 5
    {1,2,3,0,4,5,6,7},// U  6
    {3,0,1,2,4,5,6,7},// U' 7
    {2,3,0,1,4,5,6,7},// U2 8
    {0,1,2,3,5,6,7,4},// D  9
    {0,1,2,3,7,4,5,6},// D' 10
    {0,1,2,3,6,7,4,5},// D2 11
    {3,1,2,5,0,4,6,7},// F  12
    {4,1,2,0,5,3,6,7},// F' 13
    {5,1,2,4,3,0,6,7},// F2 14
    {0,7,1,3,4,5,2,6},// B  15
    {0,2,6,3,4,5,7,1},// B' 16
    {0,6,7,3,4,5,1,2} // B2 17
};
static const uint8_t route_tab_cr[18][8]={
    {0,0,2,1,0,2,1,0},// L  0
    {0,0,2,1,0,2,1,0},// L' 1
    {0,0,0,0,0,0,0,0},// L2 2
    {2,1,0,0,1,0,0,2},// R  3
    {2,1,0,0,1,0,0,2},// R' 4
    {0,0,0,0,0,0,0,0},// R2 5
    {0,0,0,0,0,0,0,0},// U  6
    {0,0,0,0,0,0,0,0},// U' 7
    {0,0,0,0,0,0,0,0},// U2 8
    {0,0,0,0,0,0,0,0},// D  9
    {0,0,0,0,0,0,0,0},// D' 10
    {0,0,0,0,0,0,0,0},// D2 11
    {1,0,0,2,2,1,0,0},// F  12
    {1,0,0,2,2,1,0,0},// F' 13
    {0,0,0,0,0,0,0,0},// F2 14
    {0,2,1,0,0,0,2,1},// B  15
    {0,2,1,0,0,0,2,1},// B' 16
    {0,0,0,0,0,0,0,0} // B2 17
};
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

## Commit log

2022-06-18 提交源代码
    [3d_print.scad, 3d_print_claw_x2.stl, 3d_print_cube_spin.stl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]
2022-06-18 修改README
2022-07-05 更新tools
2022-07-05 补充21步骤左右求解魔方的算法
2022-07-06 修改无法生成查找表的bug
2022-07-10 完成NAND FLASH驱动刷写程序
2022-07-13 添加20步左右的求解代码，经测试可以正常使用
2022-07-13 修改弹簧片3D打印文件，解决容易断裂的问题
    [3d_print_spring_x4.stl, main.scad]
2022-07-14 支持两种不同的速度，低速模式方便观察还原过程，高速模式可在7秒左右还原魔方
2022-10-18 补充弹簧组建STL文件
    [弹簧组件.stl]
2023-12-18 补充下一版本的更新计划
2023-12-18 新建 原理图与PCB
2023-12-18 上传原理图和PCB
    [BOM.xlsx]
2023-12-24 PCB & SCH & README
    [BOM.xlsx, 爪子-铣加工.scad, 爪子-铣加工x2.stl]
2023-12-30 略微降低电机速度
2023-12-30 V20结构图
    [3d_print.scad, 3d_print_main.stl, 3d_print_spring_x4.stl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]
2023-12-30 魔方机器人性能测试数据
    [魔方机器人性能测试.csv]
2023-12-30 物料清单
    [物料清单.xlsx]
2023-12-31 更新readme和bom
    [物料清单.xlsx]
2024-01-10 补充更新计划
2024-01-10 新增STEP结构图
    [cube_spin.step, fan_holder.step, 主体部分.step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]
2024-01-13 使用FIFO+PIO控制步进电机
2024-01-13 优化还原时间，平均5秒还原
2024-01-14 优化稳定性、并且增加魔方打乱、还原循环测试功能。
2024-01-16 解决魔方安装错误时，容易死机的问题
    [模仿机器人性能测试（2024-01-16）.csv]
2024-03-28 优化求解魔方的程序
2024-04-14 视频链接
2024-05-09 解决部分编译器的优化造成stepper_move_wait_all功能异常的问题
2024-05-19 开发新的算法，无需外部NAND FLASH
2024-05-21 20步左右的算法
2024-05-21 修改BOM，增加磁铁，提示100mR=0.1R
    [BOM.xlsx, 物料清单.xlsx]
2024-05-21 优化README，优化v3版本性能
2024-05-22 增加急停功能
2024-05-23 完善文档,补充预先编译好的固件
2024-05-30 修改配置文件
